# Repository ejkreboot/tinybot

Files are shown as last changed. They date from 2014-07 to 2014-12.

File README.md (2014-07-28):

tinybot
=======

Rechargeable, customizable robots inspired by https://hackaday.io/project/581-Tiny-robot-family

NOTE: This initial design is completely untested.  Please verify schematic and board prior to manufacturing boards.

The idea here is to create a education platform for embedded computing and basic robotics.  

A drawback of this design is the use of a few surface mount components.  This is to avoid use of through hole packages for MOSFETs which are relatively large.

This design incorporates a charging circuit.  Plugging in the robot to a USB charger will charge a lithium ion cell inserted into the batter holder.  This circuit is designed to charge at 100mA.

To use the robot, pager vibrator type motors must be soldered to the motor pads (one on the left, one on the right) and then hot glued in place (see https://hackaday.io/project/581-Tiny-robot-family).  The ATtiny must be programmed prior to inserting into the socket (again, see https://hackaday.io/project/581-Tiny-robot-family).

The PCB includes a prototyping area with adjacent power rails to allow adding sensors/actuators to the free pins of the ATtiny.

The ATtiny can NOT be programmed in place with this design (that would require additional circuitry to isolate the ATtiny during programming).  However, the ATtiny can be programmed on a breadboard by an Arduino running the ArduinoISP sketch (see http://www.instructables.com/id/Program-an-ATtiny-with-Arduino/).  

Please lend a hand and correct/improve the design!

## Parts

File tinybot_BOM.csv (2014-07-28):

 |  |  |  |  |  |  |  |  |  | Lots of 100 Robots (each)
PCB ID | Quant | Manufacturer Part # | Mouser # | Manufacturer | Description | Each | Total | Source | Shipping | Each | Min | Total
N/A | 1 | LIR2450 | NA |  | 3.6V 140mAh coin cell | $0.95 | $0.95 | Ebay (http://goo.gl/HYa7EU) | Free | $0.95 | 10 | $0.95
1068 | 1 | 1068 | 534-1068 | Keystone | Vertical coin cell holder | $1.79 | $1.79 | Mouser | * | $1.60 | 100 | $1.60
N/A | 1 | TinyBot 0.1 | NA | dirtypcbs.com | PCB | $1.40 | $1.40 | Dirtypcbs.com | Free | $0.62 | 40 | $0.62
N/A | 1 | ATTINY85 | 556-ATTINY85-20PU | Atmel | Microcontroller | $1.32 | $1.32 | Mouser/Digikey/Newark | * | $0.78 | 50 | $0.78
MOTOR | 2 | 9073 | NA | Dowonsol | Pager type motor | $0.83 | $1.66 | Aliexpress (http://goo.gl/tIYG5n) | Free | $0.64 | 50 | $1.28
MCP | 1 | MCP73831 | 579-MCP73831T-2ACIOT | Microchip | Battery charge controller | $0.60 | $0.60 | Mouser/Digikey/Newark | * | $0.42 | 100 | $0.42
Q1 | 1 | NDS332P | 512-NDS332P | Fairchild | P Channel MOSFET | $0.52 | $0.52 | Mouser/Digikey/Newark | * | $0.14 | 100 | $0.14
C1, C3 | 2 | FK18X5R1A475K | 810-FK18X5R1A475K | TDK | 4.7uF ceramic capacitor | $0.32 | $0.64 | Mouser/Digikey/Newark/Radioshack | * | $0.10 | 100 | $0.20
C2 | 1 | FK18X5R1E105K | 810-FK18X5R1E105K | TDK | 1uF ceramic capacitor | $0.28 | $0.28 | Mouser/Digikey/Newark/Radioshack | * | $0.09 | 100 | $0.09
SOCKET | 1 | 1-2199298-2 | 571-1-2199298-2 | TE Connectivity | DIP Socket | $0.10 | $0.10 | Mouser/Digikey/Newark/Radioshack | * | $0.08 | 100 | $0.08
Q2, Q3 | 2 | 2N7002E | 863-2N7002ET1G | ON Semi | N Channel MOSFET | $0.14 | $0.28 | Mouser/Digikey/Newark | * | $0.04 | 100 | $0.08
RED | 1 | LTL2R3KRD-EM | 859-LTL2R3KRD-EM | Lite-on | 5mm Red LED | $0.08 | $0.08 | Mouser/Digikey/Newark/Radioshack | * | $0.06 | 100 | $0.06
R1 | 1 | MF1/4DC1000F | 660-MF1/4DC1000F | KOA Speer | 100 Kohm resistor | $0.06 | $0.06 | Mouser/Digikey/Newark/Radioshack | * | $0.04 | 100 | $0.04
R2 | 1 | MF1/4DC4700F | 660-MF1/4DC4700F | KOA Speer | 470 ohm resistor | $0.05 | $0.05 | Mouser/Digikey/Newark/Radioshack | * | $0.04 | 100 | $0.04
R3 | 1 | MF1/4DC1002F | 660-MF1/4DC1002F | KOA Speer | 10 Kohm resistor | $0.05 | $0.05 | Mouser/Digikey/Newark/Radioshack | * | $0.04 | 100 | $0.04
GRAND TOTAL PER TINYBOT |  |  |  |  |  |  | $9.78 |  |  |  |  | $6.42
 | * | Shipping from Mouser for 10 tinybots worth of supplies to the US is roughly 5.00

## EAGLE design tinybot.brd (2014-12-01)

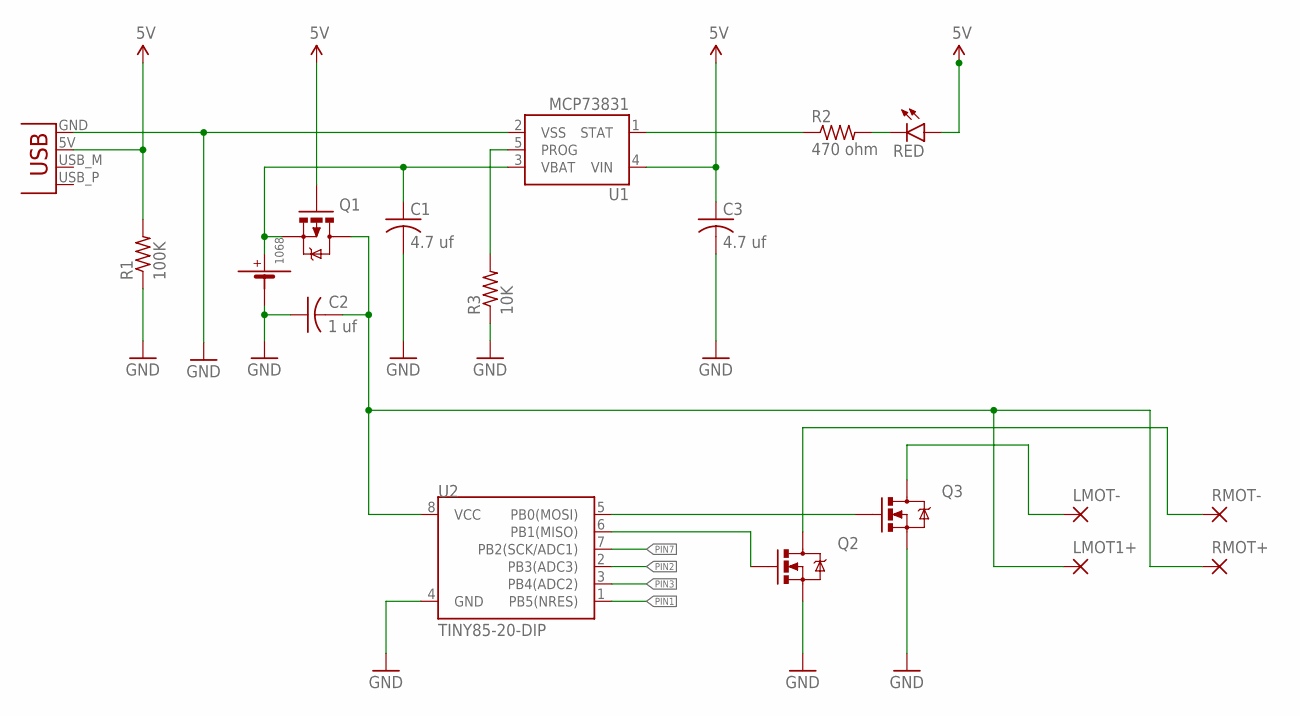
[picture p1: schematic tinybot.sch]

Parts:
C1, C3: 4.7 uf; C025-025X050
C2: 1 uf; C025-025X050
JP1: USBPCB; USB-A-PCB
LMOT1+: WIREPADSMD1,27-254; SMD1,27-2,54
LMOT-: WIREPADSMD1,27-254; SMD1,27-2,54
Q1: MOSFET-PCHANNEL; SOT23-3
Q2, Q3: 2N7002PW; SOT23
R1: 100K; 0204/5
R2: 470 ohm; 0204/5
R3: 10K; 0204/5
RED: LED3MM
RMOT+: WIREPADSMD1,27-254; SMD1,27-2,54
RMOT-: WIREPADSMD1,27-254; SMD1,27-2,54
U1: MCP73831; SOT23-5
U2: TINY85-20-DIP; DIP08
U$1: 1068; KEYSTONE1068

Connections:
5V: C3.1, JP1.5V (VBUS), Q1.1 (G), R1.2, RED.A, U1.4 (VIN)
GND: C1.2, C2.1, C3.2, JP1.GND, Q2.2 (S), Q3.2 (S), R1.1, R3.1, U1.2 (VSS), U2.4 (GND), U$1.NEG (-)
unnamed: R2.2, RED.K (C)
unnamed: R2.1, U1.1 (STAT)
unnamed: Q3.1 (G), U2.5 (PB0(MOSI))
unnamed: Q2.1 (G), U2.6 (PB1(MISO))
unnamed: LMOT-.1, Q3.3 (D)
unnamed: Q2.3 (D), RMOT-.1
unnamed: R3.2, U1.5 (PROG)
PIN1: U2.1 (PB5(NRES))
PIN2: U2.2 (PB3(ADC3))
PIN3: U2.3 (PB4(ADC2))
PIN7: U2.7 (PB2(SCK/ADC1))
VBAT: C1.1, Q1.2 (S), U1.3 (VBAT), U$1.POS (+)
VCC: C2.2, LMOT1+.1, Q1.3 (D), RMOT+.1, U2.8 (VCC)

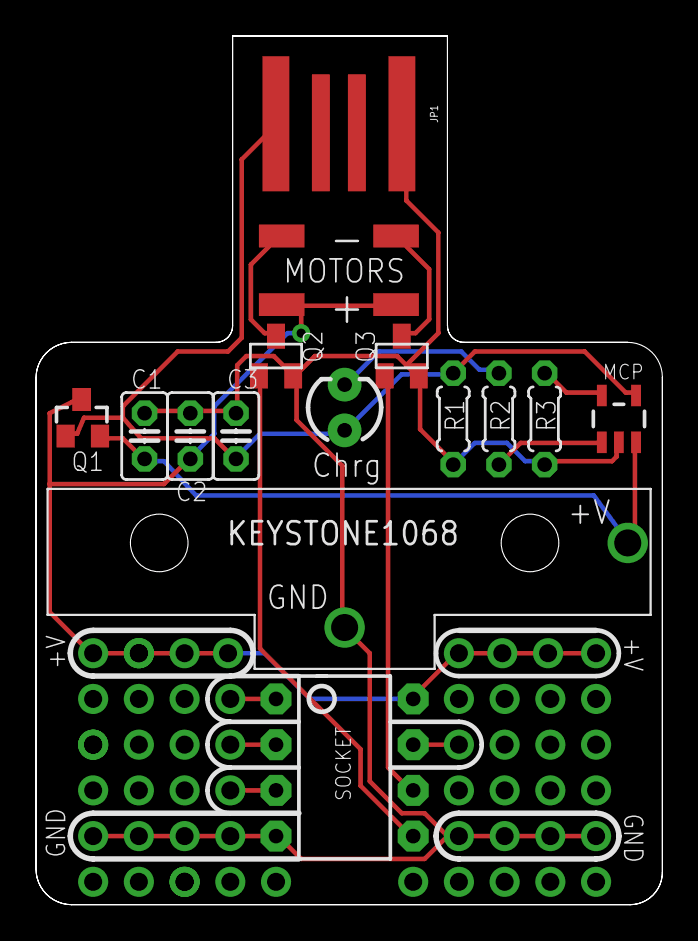
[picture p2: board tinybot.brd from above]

Board: 2 copper layers, 34.8 x 48.3 mm, 18 parts (0 on the bottom side), 11 nets.

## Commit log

2014-07-23 Added board, schematic, and library files
    [tinybot.brd, tinybot.sch]
2014-07-23 Updated board labels, added BOM
    [tinybot.brd, tinybot.csv]
2014-07-24 update milling layer with board outline
    [tinybot.brd]
2014-07-24 fixed mosfet wiring error
    [tinybot.brd]
2014-07-25 fixed motor mosfet wiring (again)
    Still had it wrong! Motor mosfets connected to 5V (from USB), not VCC.
    Now fixed.
    Also added logo/name/url to bottom silk!
    [tinybot.brd, tinybot.sch]
2014-07-25 Updated BOM (tinybot.csv)
    [tinybot.csv]
2014-07-26 Updated BOM
    Update BOM, now in both excel and csv formats
    [tinybot.csv, tinybot_BOM.csv, tinybot_BOM.xlsx]
2014-07-28 updated BOM
    [tinybot_BOM.csv, tinybot_BOM.xlsx]
2014-07-28 Decreased charge current from 500mA to 100mA
    R3 changed from 2K to 10K
    [tinybot.brd, tinybot.sch, tinybot_BOM.csv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]
2014-07-28 Update README to reflect lower charge current
2014-12-01 improved mosfet pad layout and corrected battery holder hole size
    [tinybot.brd, tinybot.sch]

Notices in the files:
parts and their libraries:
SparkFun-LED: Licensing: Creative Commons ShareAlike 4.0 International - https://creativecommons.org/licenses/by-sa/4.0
